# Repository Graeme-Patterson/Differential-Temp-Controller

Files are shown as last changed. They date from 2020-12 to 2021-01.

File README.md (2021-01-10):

# Differential-Temp-Controller

This is my differential temperature controller with Wi-Fi interface and Touch screen.

The idea behind this controller was to minimise the heating cost of keeping my workshop/mancave warm in Canberra Australia winters. After recently installing a solar electricity system on our house my thoughts were about how I could use the heat from the sun to warm my workshop.
The design was to heat air in long black plastic tubes mounted in a glass fronted box in a sunny location on the roof or wall of the workshop and use a low voltage fan to move air from outside, through the plastic tubes to warm the air and blow this into the workshop. To ensure that heating is achieved and to accound for any temperature drop getting the warmed air into the workshop, I needed a device that measured the temperature at the source and at the destination. I also wanted to have control over the device from inside my house and local control with visual display.

The final result uses a 2.8" ILI9341 TFT SPI display sourced from eBay (China) and an ESP8266/NodeMCU/ESP12-E device mounted on a custom PCB using a simple relay output to control a fan. Power is via a DC barrel connector (with ideas that this could be via Solar). The temperature sensors are low cost waterproof 10k NTC Thermistors, again sourced from eBay.

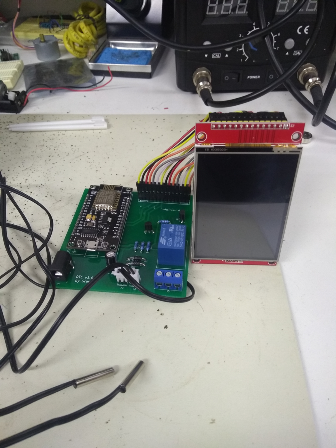
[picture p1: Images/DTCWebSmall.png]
DTC Pic

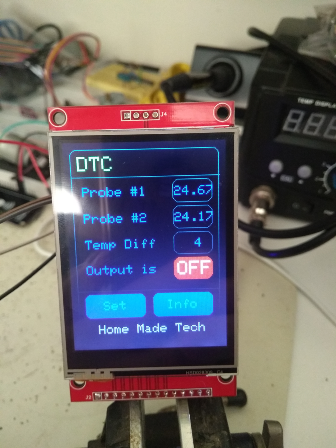
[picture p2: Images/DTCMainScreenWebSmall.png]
DTC Interface

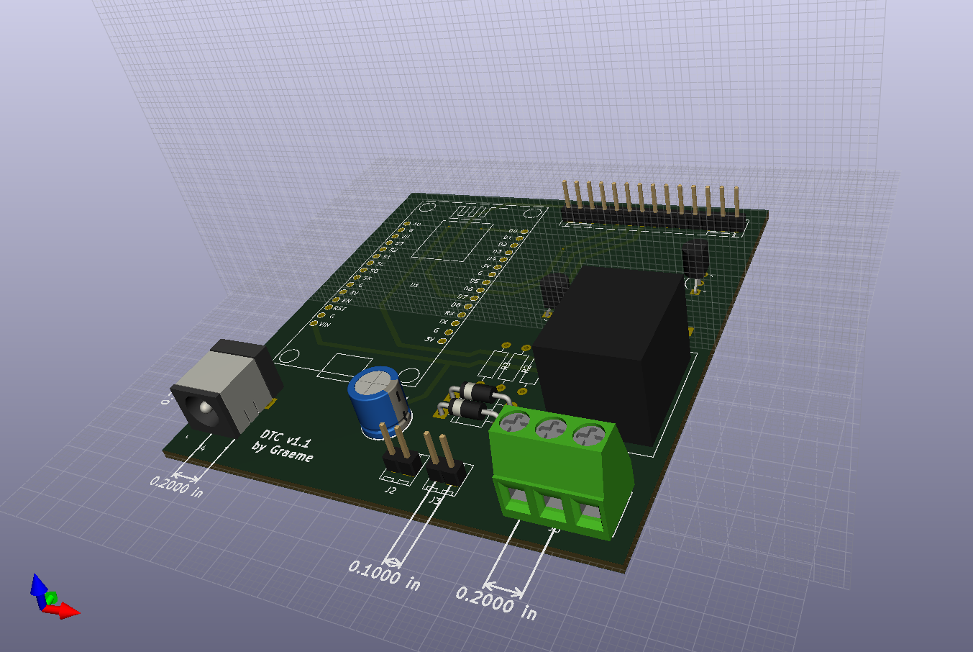
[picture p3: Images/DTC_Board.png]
3D View


- [DTC Overview](/README.md)
- [How to make one](/HowToMake.md)
- [Operation instructions](/Operation.md)
- [Connecting it up](/connecting.md)

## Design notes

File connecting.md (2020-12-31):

# Connecting it all up

Connect the DTC as follows:

Power the device from any DC source 5V source via the power supply jack. The jack will be centre pin positive.

NTC thermistors are plugged in to J2 and J3 on the PCB. Polarity is not important for these devices.

Connect your fan in series with the centre and left most pins on the 3 way connector relay output.

## A word of warning

If you choose to power the external fan from 110/240V via the onboard relay, **you do so at your own risk.** While the relay is rated for this voltage and the PCB traces have adequate separation from the other traces, this voltage is dangerous and should only be attempted by suitably qualified/experienced people.

- [DTC Overview](/README.md)
- [How to make one](/HowToMake.md)
- [Operation instructions](/Operation.md)
- [Connecting it up](/connecting.md)

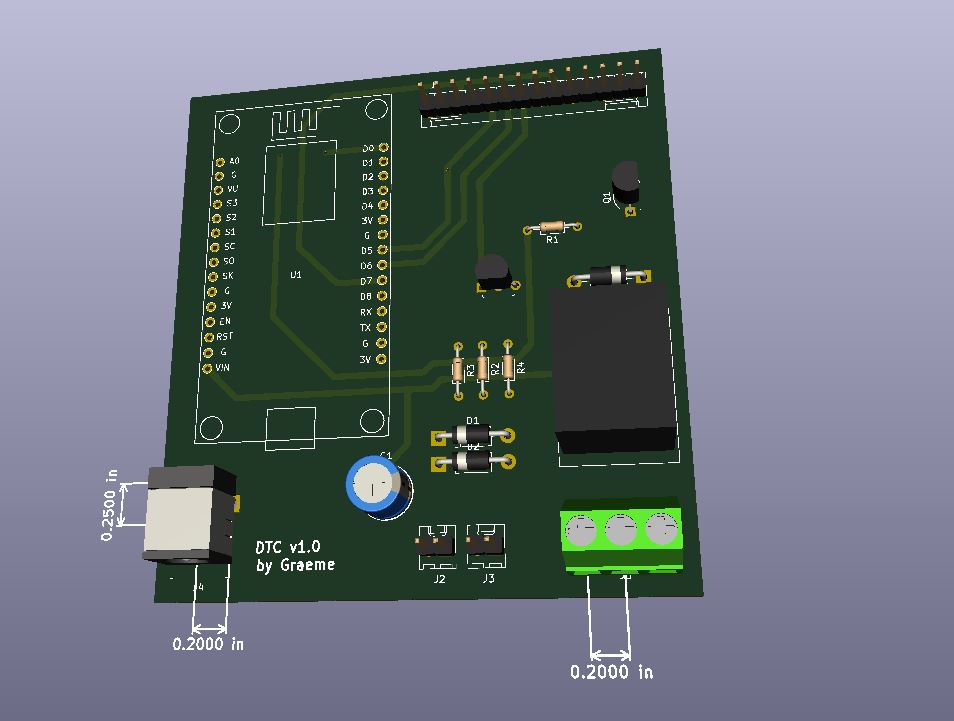
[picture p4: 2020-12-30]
PCB-KiCAD/DTC/Capture.JPG

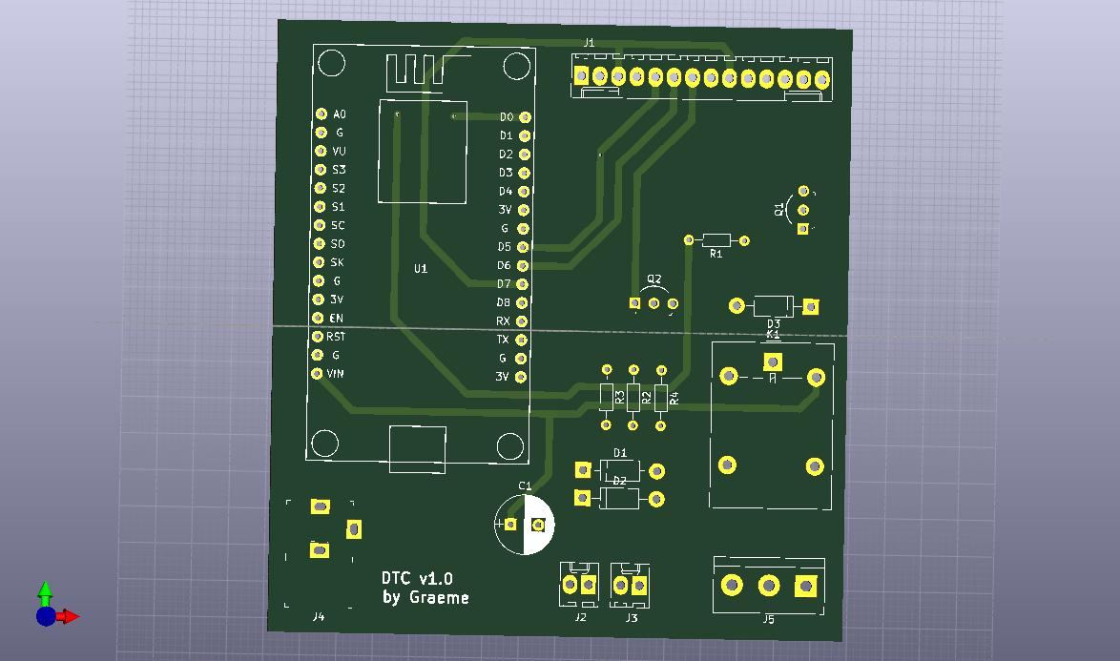
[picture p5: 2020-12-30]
PCB-KiCAD/DTC/The board.jpg

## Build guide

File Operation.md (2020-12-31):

# Operation

The DTC has only 3 screens availavle on the touch screen.

1. Main screen.
2. Set differential temp screen.
3. Information screen

When you are first using the DTC, you will need to start with the touch screen.

The main screen provides details of the temperatures of the two probes, the configured temperature difference as well as the current output status. In addition, you can access the Set screen and the Information screen.

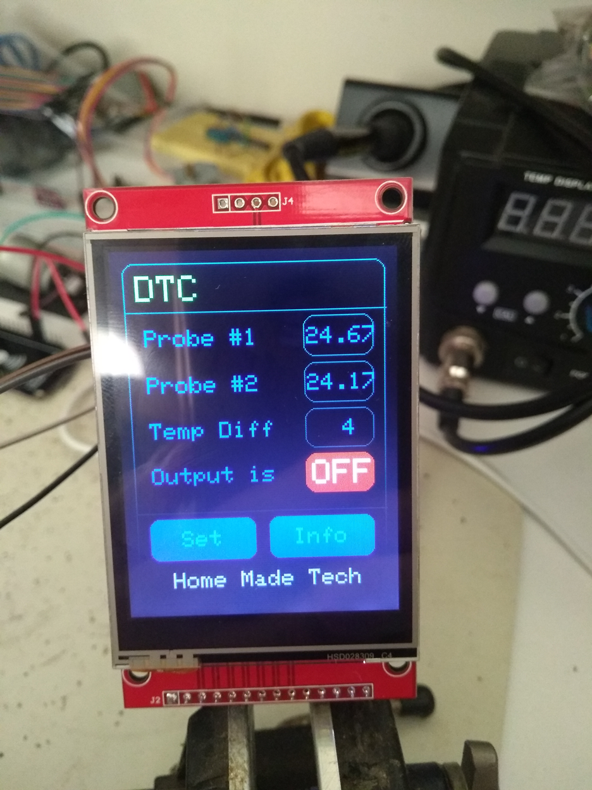
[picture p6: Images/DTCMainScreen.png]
Main screen


The Set differential temperature screen provides you the ability to adjust the temperature difference between the probes that will turn the output on. It is a simple up/down button operation with the "Save" button saving the value to memory. As expected the "Home" button will take you back to the main screen.

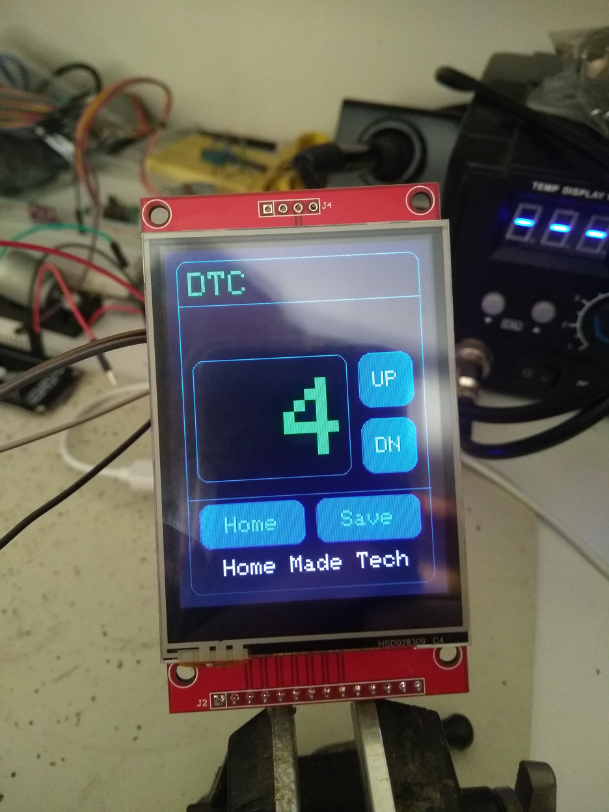
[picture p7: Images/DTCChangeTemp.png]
Set Differential Temperature Screen


The last screen is the Information screen. This screen provides you with easily accessible details allowing you to connect to the web interface from a browser and shows the chip Id which is used as a basic password allowing a user to configure the temperature differential from the browser. To connect to the web interface from a browser, simply type "http://\<IP Address>" into the address bar. 

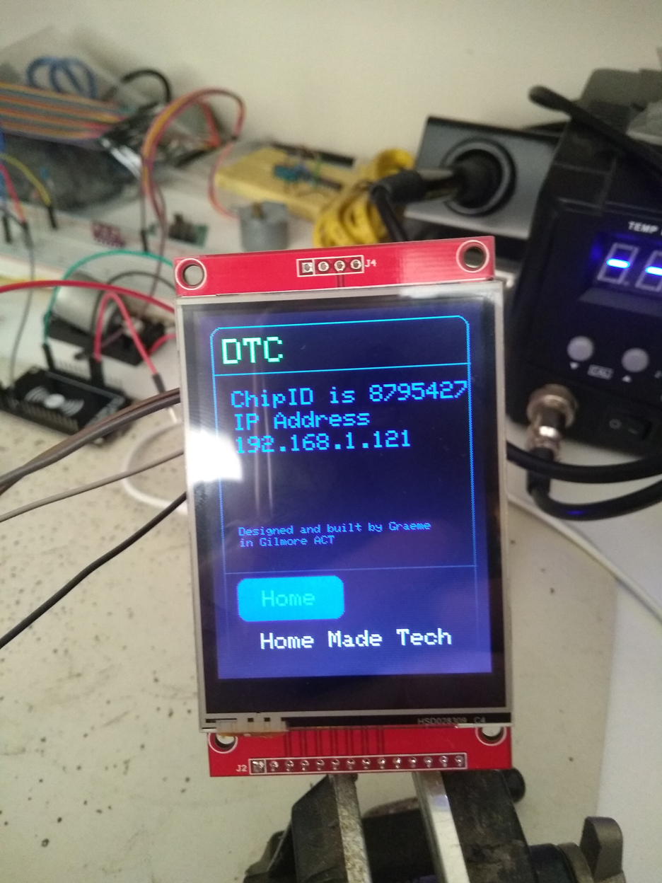
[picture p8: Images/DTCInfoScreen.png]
Information Screen


## Using the web interface

As was just mentioned, you will need to first obtain the IP address and Chip ID of the ESP device first and navigate to "http://\<IP Address>". Here you will be presented with a "functional" display allowing you to set the differential temperature of the controller only. 

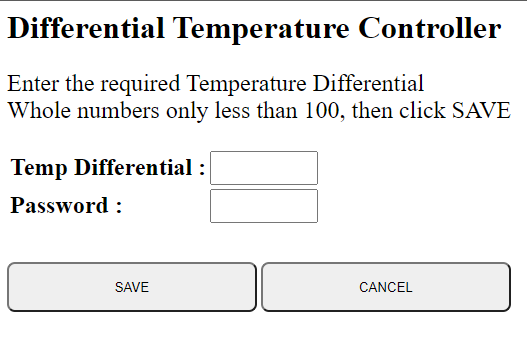
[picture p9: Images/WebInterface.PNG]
Web Interface


Simply enter the required temperature differential, enter the value of teh ChipId as the password and click save.
That's it. It's fairly simple and functional.

## A word of warning

If you choose to power the external fan from 110/240V via the onboard relay, **you do so at your own risk.** While the relay is rated for this voltage and the PCB traces have adequate separation from the other traces, this voltage is dangerous and should only be attempted by suitably qualified/experienced people.

- [DTC Overview](/README.md)
- [How to make one](/HowToMake.md)
- [Operation instructions](/Operation.md)
- [Connecting it up](/connecting.md)

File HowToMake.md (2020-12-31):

# How to make your DTC

You will need to gather all the required parts first.

Parts List

- 1 x ESP8266/NodeMCU/ESP12-E
- 3 x 1N4004 (or similar)  Diodes
- 1 x SRD-05VDC-SL-C SPDT 5V Relay
- 1 x DC-005 Power Supply Jack
- 2 x 10k NTC Waterproof Thermistor
- 1 x 2.8" TFT SPI LCD Touch Panel (ILI9341 240x320 5V/3.3V)
- 1 x BC337 transistor
- 1 x BC327 transistor
- 4 x 10k 1/4W MF ressitors
- 1 x 100uF 25V electrolytic capacitor
- 2 x 2 pin 0.1" pitch headers
- 1 x 14 pin 0.1" pitch header
- 1 x 3 way 0.2" pitch screw terminal
- 1 x PCB (you'll need to have this manufactured. I used JLCPCB - 5 boards for $2)

As I mentioned above, I used JLCPCB (https://jlcpcb.com) to have my PCB's made. They provided me with great service at an awesome price, $2 for 5 pcbs - double sided with solder mask and silk screened in your choice of colour.

Upload the DTCWiFiDisplay.ino sketch to your ESP8266.

Assemble the PCB as shown in [PCB Component Placement](/PCB/DTC_Component_Placement.pdf)

## First Run

On first run, the ESP device will not know about your WiFi network and will go into AP mode. Use you phone/laptop etc to connect to the ESP device AP and select/provide your WiFi network details. Restart the device and it should now be connected to your WiFi.

After you have your DTC on your WiFi network, take a look at [Operation instructions](/Operation.md) to see how to use it.

- [DTC Overview](/README.md)
- [How to make one](/HowToMake.md)
- [Operation instructions](/Operation.md)
- [Connecting it up](/connecting.md)

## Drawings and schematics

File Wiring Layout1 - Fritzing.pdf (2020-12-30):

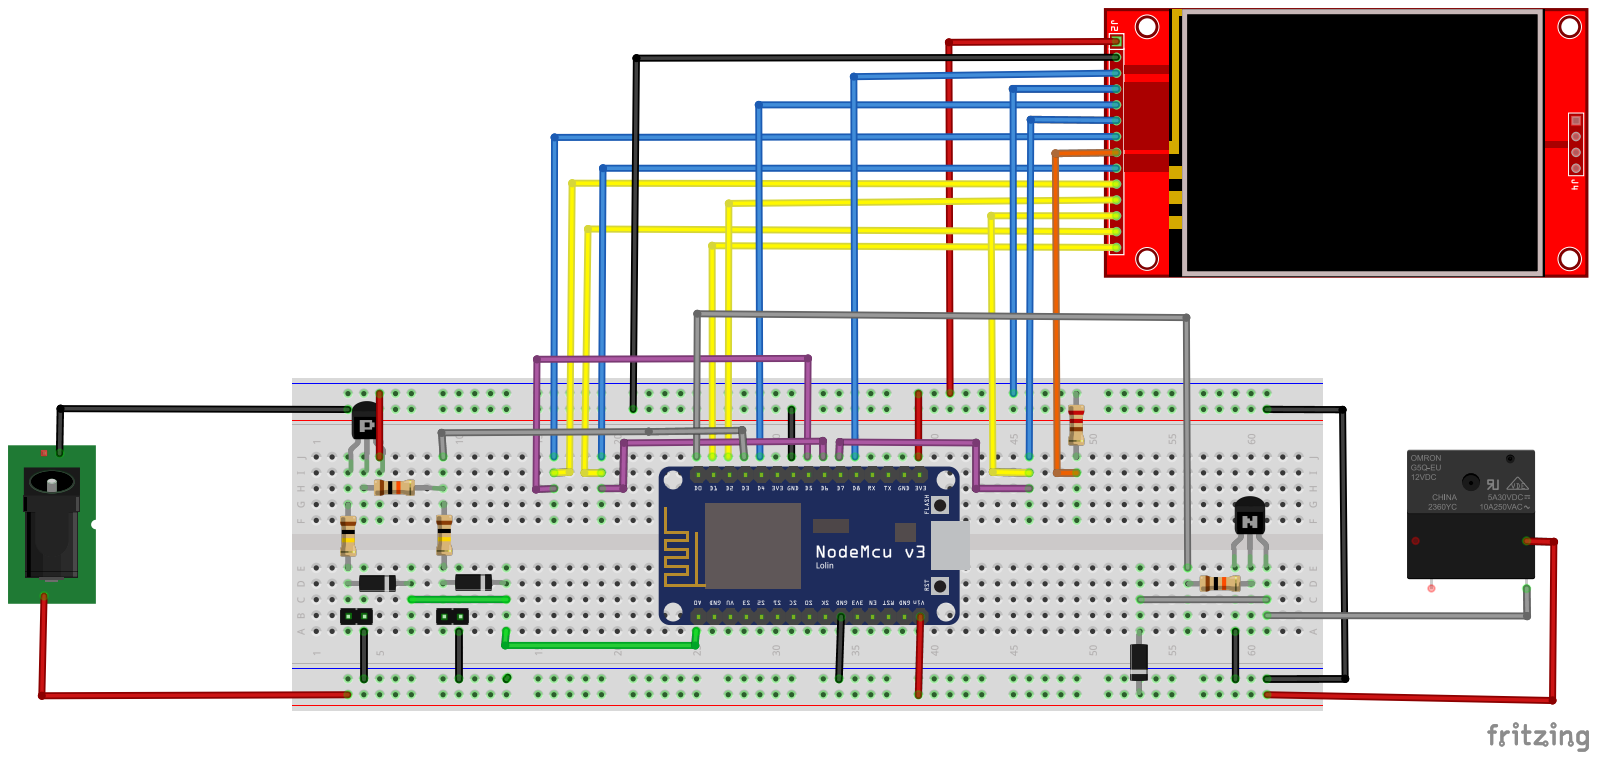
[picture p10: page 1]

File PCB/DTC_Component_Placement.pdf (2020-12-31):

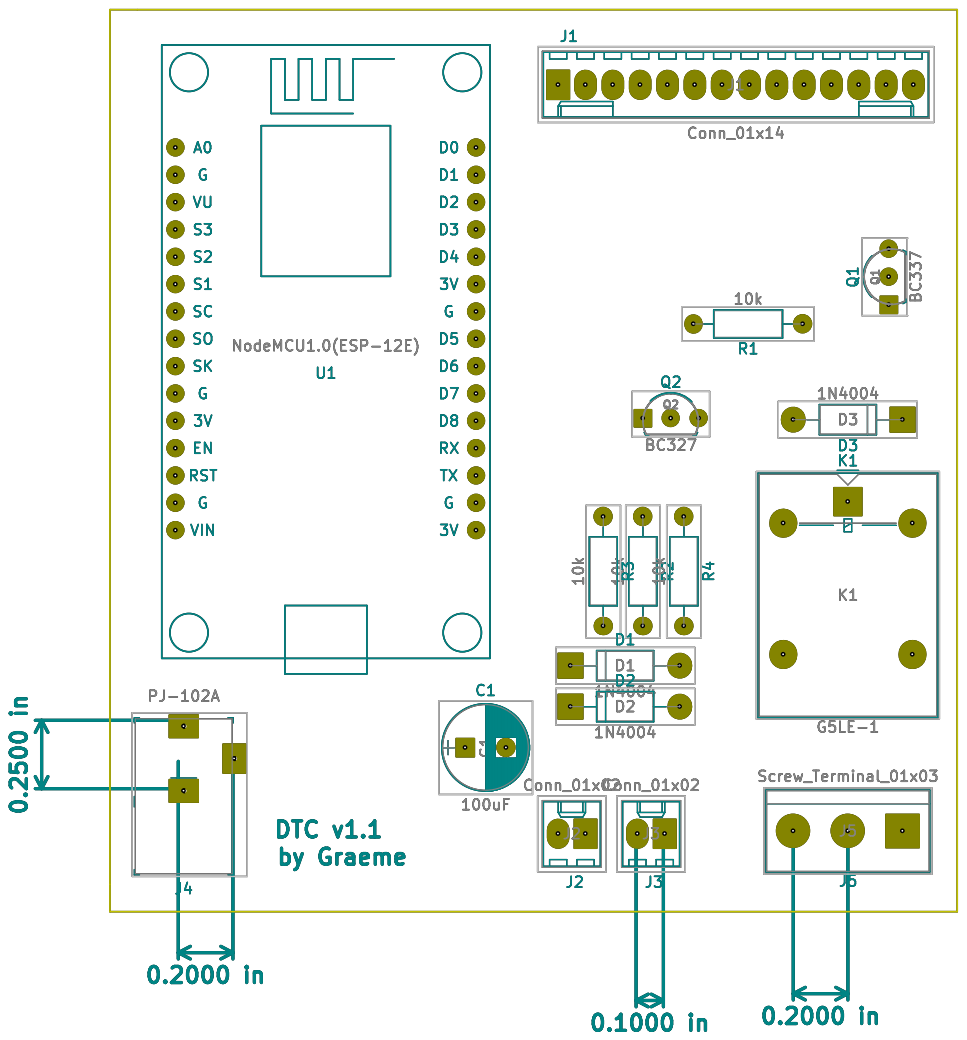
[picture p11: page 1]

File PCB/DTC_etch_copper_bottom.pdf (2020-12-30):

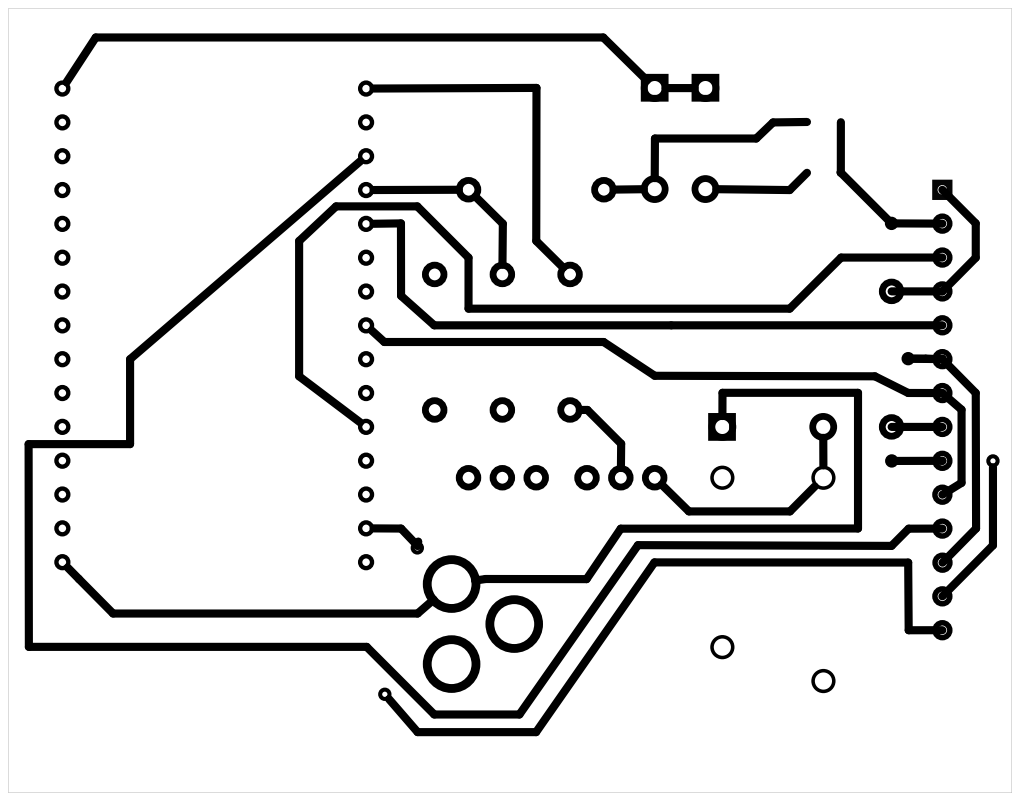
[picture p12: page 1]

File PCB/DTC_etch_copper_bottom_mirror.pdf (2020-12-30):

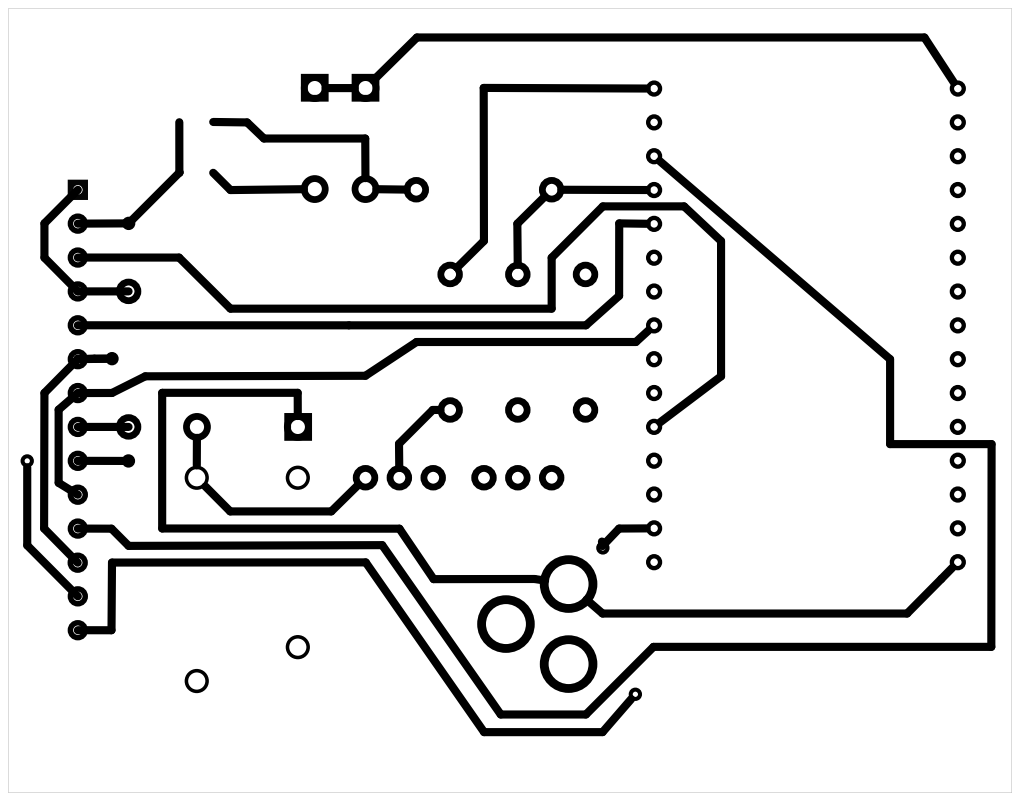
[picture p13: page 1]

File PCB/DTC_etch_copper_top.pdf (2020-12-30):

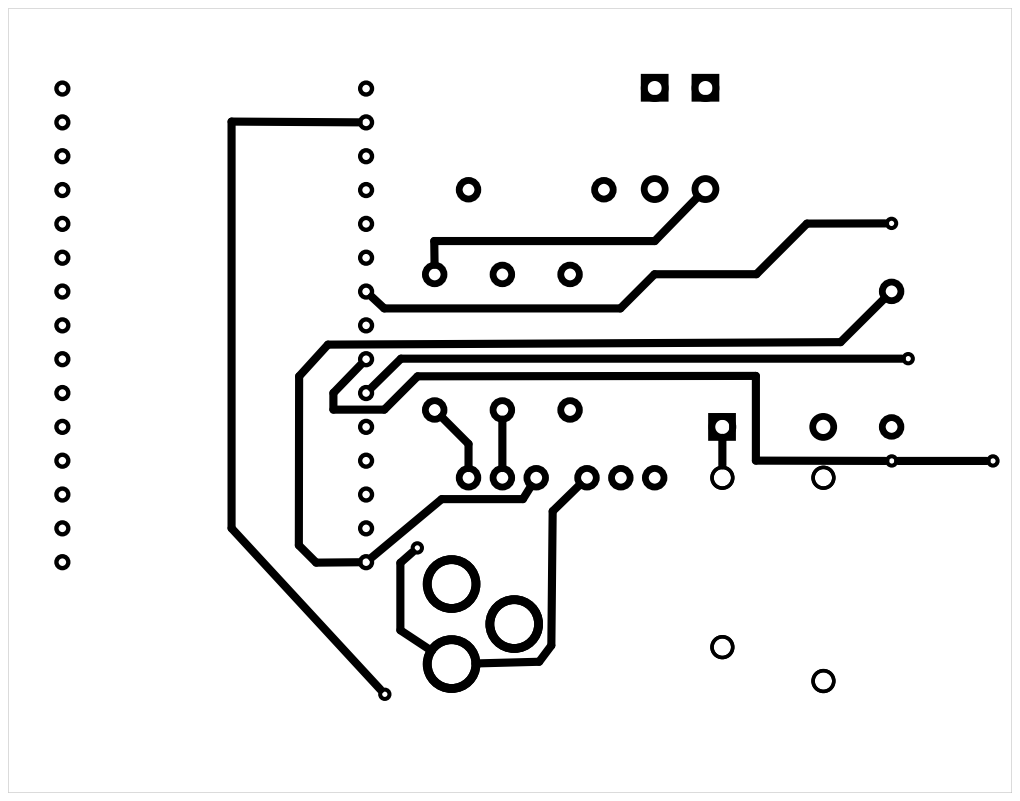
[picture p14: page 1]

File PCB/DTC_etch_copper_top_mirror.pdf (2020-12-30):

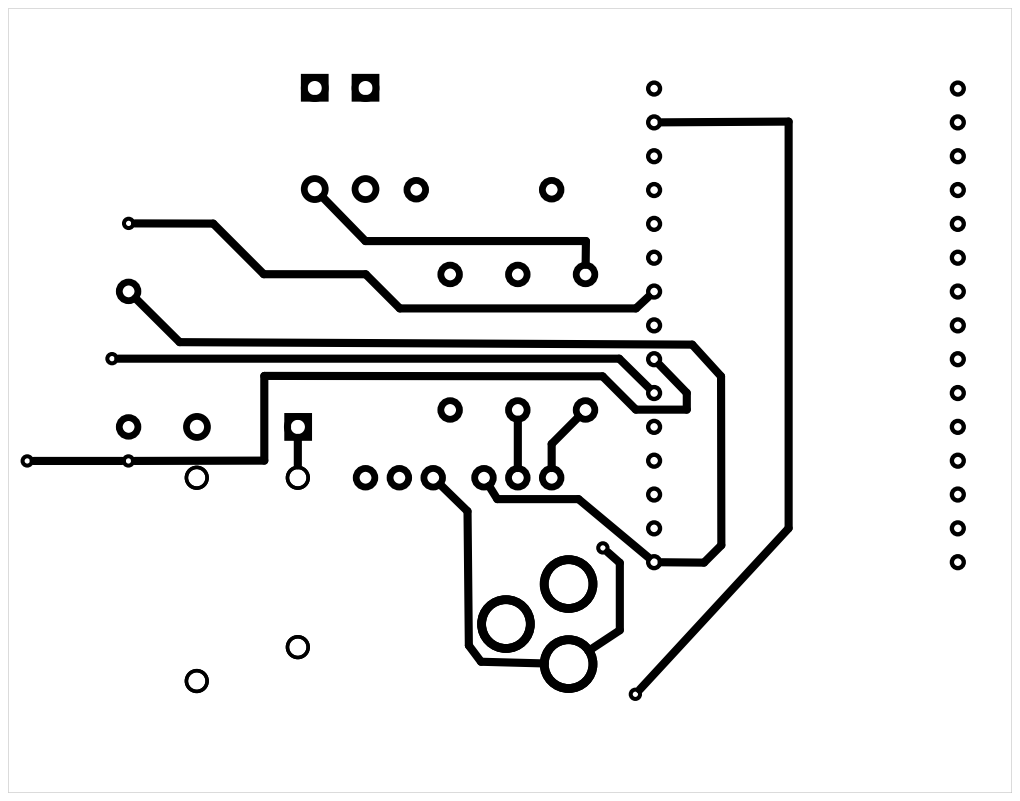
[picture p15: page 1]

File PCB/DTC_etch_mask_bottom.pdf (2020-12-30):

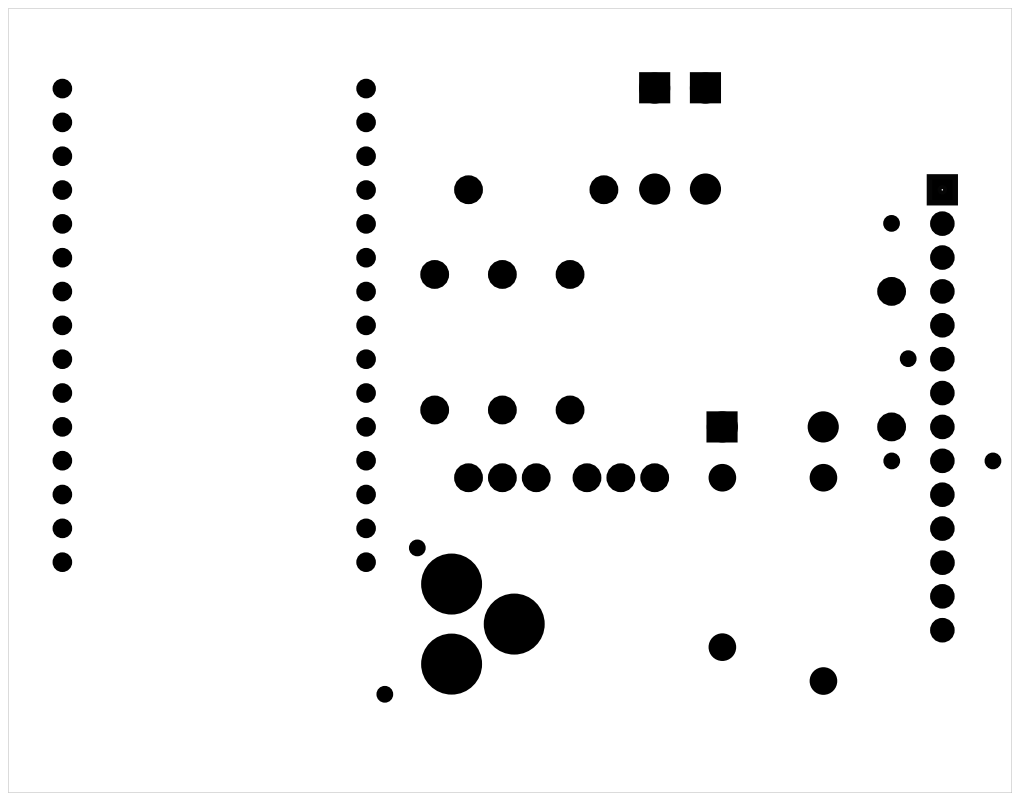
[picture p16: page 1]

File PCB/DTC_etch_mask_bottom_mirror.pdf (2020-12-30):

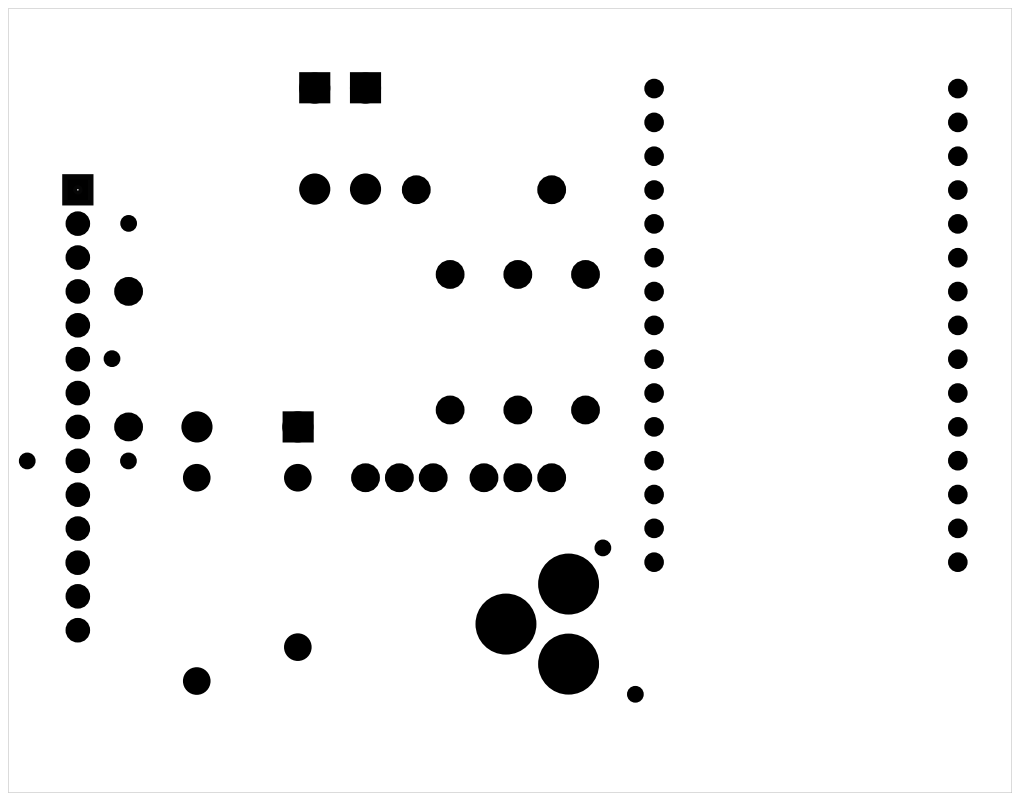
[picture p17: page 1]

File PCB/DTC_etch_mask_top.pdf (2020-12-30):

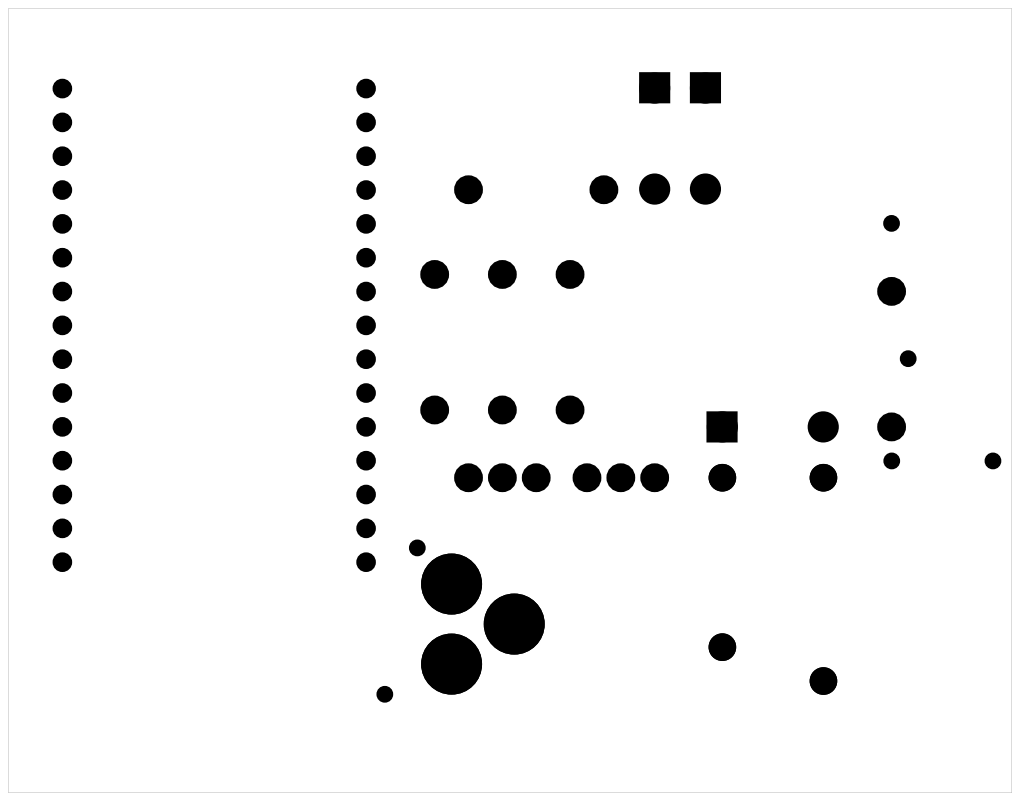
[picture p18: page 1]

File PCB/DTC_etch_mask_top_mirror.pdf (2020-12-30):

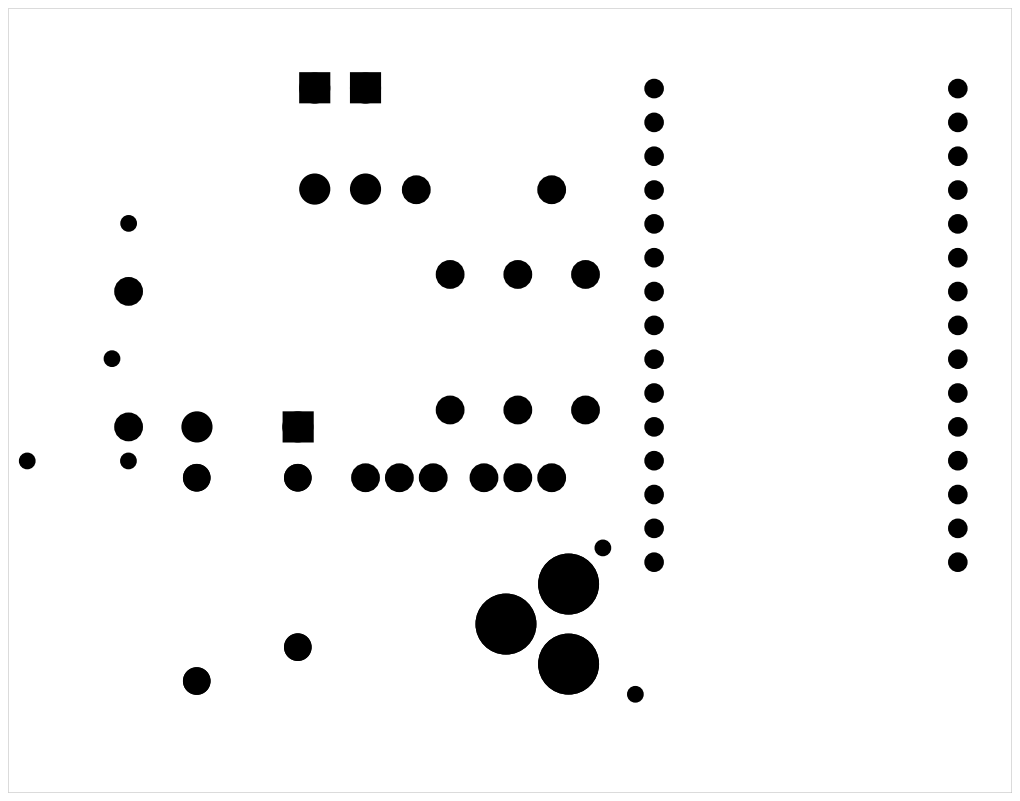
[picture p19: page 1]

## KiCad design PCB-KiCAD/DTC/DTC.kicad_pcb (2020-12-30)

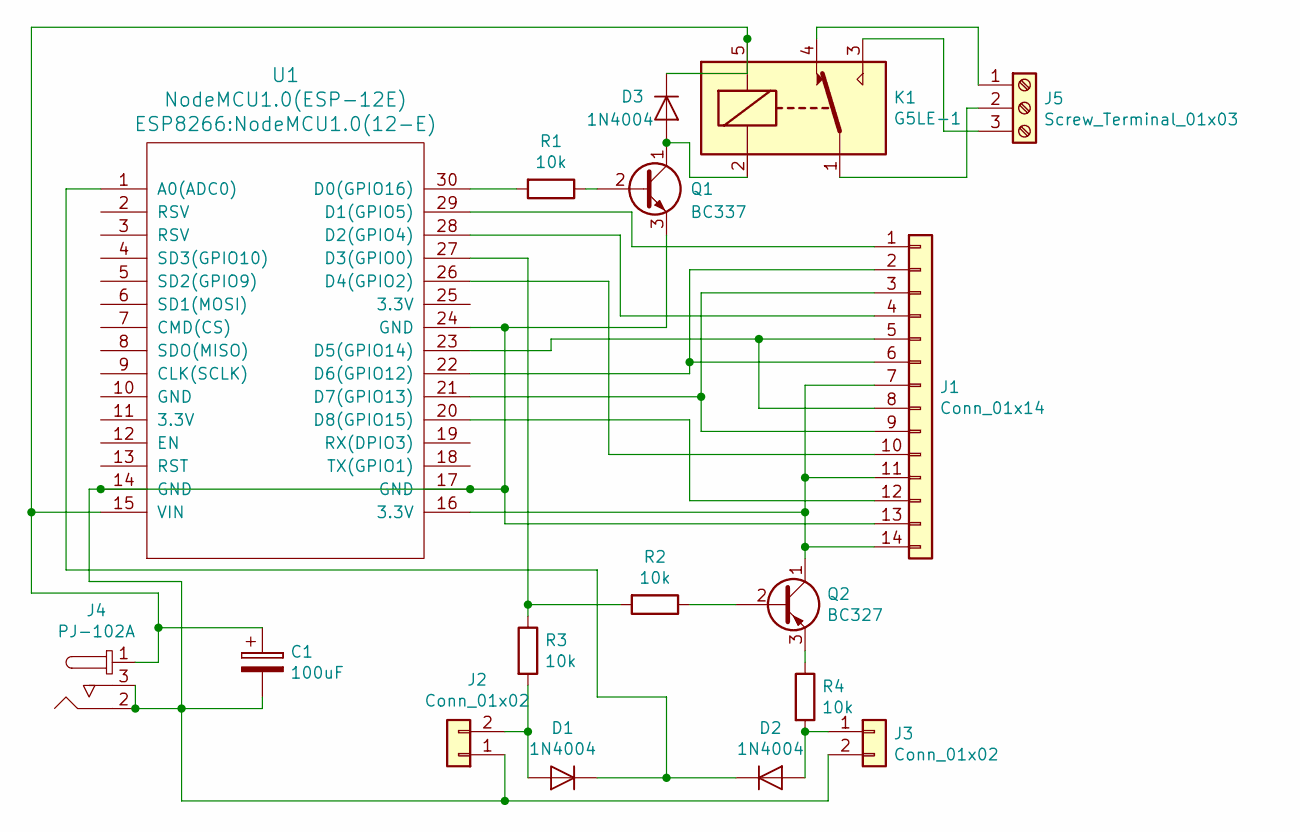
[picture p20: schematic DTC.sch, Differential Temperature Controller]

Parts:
C1: 100uF; CP_Radial_D8.0mm_P3.80mm
D1, D2, D3: 1N4004; D_DO-41_SOD81_P10.16mm_Horizontal
J1: Conn_01x14; Molex_KK-6410-14_14x2.54mm_Straight
J2, J3: Conn_01x02; Molex_KK-6410-02_02x2.54mm_Straight
J4: PJ-102A; Barrel_Jack_5.5mmODx2.1mmID_PJ-102A; MPN PJ-102A; Digi-Key_PN CP-102A-ND
J5: Screw_Terminal_01x03; TerminalBlock_bornier-3_P5.08mm
K1: G5LE-1; Relay_SPDT_OMRON-G5LE-1
Q1: BC337; TO-92-3_Formed_Leads
Q2: BC327; TO-92-3_Formed_Leads
R1, R2, R3, R4: 10k; R_Axial_DIN0204_L3.6mm_D1.6mm_P7.62mm_Horizontal
U1: NodeMCU1.0(ESP-12E); NodeMCU1.0(12-E)

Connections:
unnamed: C1.1, D3.1 (K), J4.1, K1.5, U1.15 (VIN)
unnamed: C1.2, J1.13, J2.1, J3.2, J4.2, J4.3, Q1.3 (E), U1.14 (GND), U1.17 (GND), U1.24 (GND)
unnamed: D1.1 (K), D2.1 (K), U1.1 (A0(ADC0))
unnamed: D1.2 (A), J2.2, R3.2
unnamed: D2.2 (A), J3.1, R4.2
unnamed: D3.2 (A), K1.2, Q1.1 (C)
unnamed: J1.1, U1.29 (D1(GPIO5))
unnamed: J1.2, J1.6, U1.22 (D6(GPIO12))
unnamed: J1.3, J1.9, U1.21 (D7(GPIO13))
unnamed: J1.4, U1.28 (D2(GPIO4))
unnamed: J1.5, J1.8, U1.23 (D5(GPIO14))
unnamed: J1.10, U1.26 (D4(GPIO2))
unnamed: J1.7, J1.11, J1.14, Q2.1 (C), U1.16 (3.3V)
unnamed: J1.12, U1.20 (D8(GPIO15))
unnamed: J5.1, K1.4
unnamed: J5.2, K1.1
unnamed: J5.3, K1.3
unnamed: Q1.2 (B), R1.1
unnamed: Q2.2 (B), R2.1
unnamed: Q2.3 (E), R4.1
unnamed: R1.2, U1.30 (D0(GPIO16))
unnamed: R2.2, R3.1, U1.27 (D3(GPIO0))

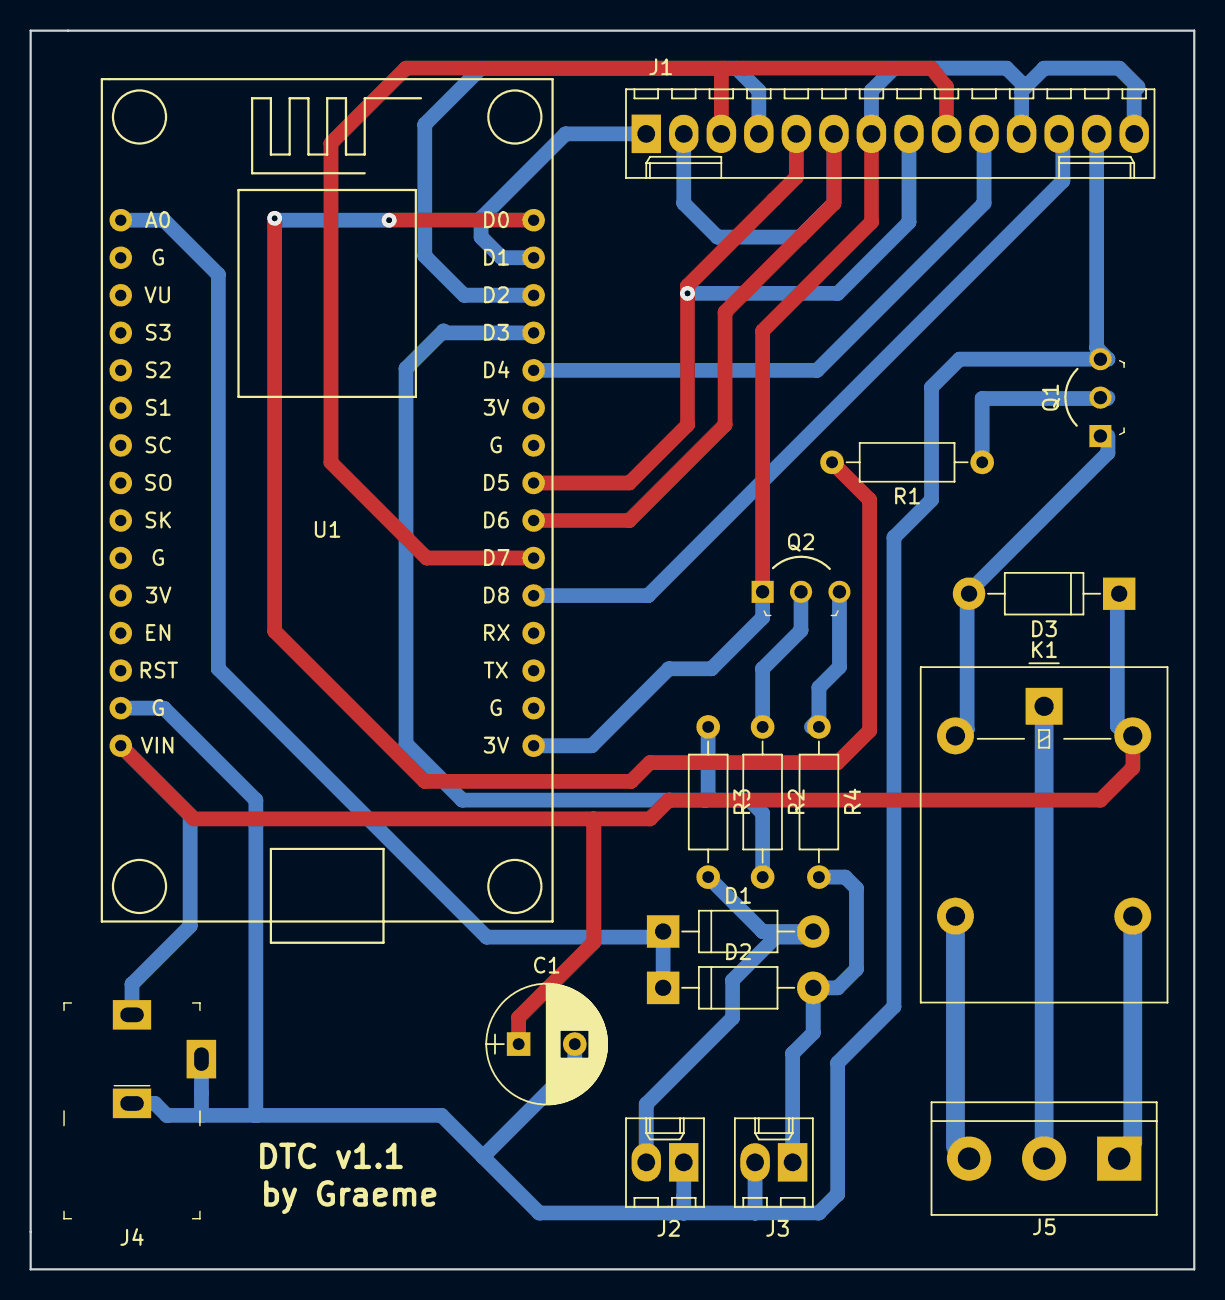
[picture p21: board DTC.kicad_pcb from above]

Board: 2 copper layers, 78.7 x 83.8 mm, 17 parts (0 on the bottom side), 22 nets.

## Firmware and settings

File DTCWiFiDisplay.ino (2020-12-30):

#include <ESP8266WiFi.h>          //https://github.com/esp8266/Arduino
#include <DNSServer.h>
#include <ESP8266WebServer.h>
#include <WiFiManager.h>          //https://github.com/tzapu/WiFiManager
#include <EEPROM.h>
#include <Arduino.h>
#include <SPI.h>
#include <Adafruit_ILI9341esp.h>
#include <Adafruit_GFX.h>
#include <XPT2046.h>

// which analog pin to connect
#define THERMISTORPIN A0         
// resistance at 25 degrees C
#define THERMISTORNOMINAL 10000      
// temp. for nominal resistance (almost always 25 C)
#define TEMPERATURENOMINAL 25   
// how many samples to take and average to smooth thing sout
#define NUMSAMPLES 5
// The beta coefficient of the thermistor (usually 3000-4000)
#define BCOEFFICIENT 3950
// the value of the 'other' resistor
#define SERIESRESISTOR 10000    
#define Thermistor0 0
#define Thermistor1 1
#define ThermistorSelect D3
//#define DIFFERENTIAL 5
#define DIODECOMPENSATION 100
#define RELAYOUTPUT D0
// For the esp shield, these are the default.
#define TFT_DC 2
#define TFT_CS 15
#define HOME 1
#define SET 2
#define INFO 3

Adafruit_ILI9341 tft = Adafruit_ILI9341(TFT_CS, TFT_DC);
XPT2046 touch(/*cs=*/ 4, /*irq=*/ 5);

Adafruit_GFX_Button homeButton;
Adafruit_GFX_Button upButton;
Adafruit_GFX_Button downButton;
Adafruit_GFX_Button saveButton;
Adafruit_GFX_Button setButton;
Adafruit_GFX_Button infoButton;

String webPage,notice,homeWebPage,message;
int DIFFERENTIAL;
int unsavedDifferential;
float Temp0;
float Temp1;
int samples[NUMSAMPLES];
int address = 0;
int relayState = 0;
int measurePeriod=10000;  // this is 10 seconds
unsigned long time_now = 0;
int screen = 1;
static uint16_t prev_x = 0xffff, prev_y = 0xffff;

ESP8266WebServer server(80);

const char htmlPage[]PROGMEM=R"=====(
<!DOCTYPE html>
<html><head><title>DTC-SET</title></head>
<body>
<h1>Differential Temperature Controller</h1><font size="5">
<FORM METHOD="POST" action="/Save">
<p> Enter the required Temperature Differential
<br> Whole numbers only less than 100, then click SAVE</p></font>
<table>
    <tr
        ><th style="font-size: 24px; text-align: left">Temp Differential : </th>
        <th><input type="text" size="4" name="myText" value="" autofocus style="font-size:24px;" ></th>
    </tr>
    <tr>
        <th style="font-size: 24px; text-align: left">Password          :</th>
        <th><input type="password" size="4" name="myCheck" value=""  style="font-size:24px"></th>
    </tr>
</table>
<br><br>
<th><input type="submit" value="SAVE" style="height:50px; width:250px;border-radius: 8px"></th>
<input type="button" value="CANCEL" style="height:50px; width:250px;border-radius: 8px" onclick="location.href='/'" />
</form>
</body>
</html>
)=====";

void handleRoot()
{
  homeWebPage = "<!DOCTYPE html><html><head><title>DTC</title><meta http-equiv=\"refresh\" content=\"30\" /></head><body><h1>Differential Temperature Controller</h1><font size=\"5\"><p><pre>Temp Sensor 0     : ";
  homeWebPage += Temp0;
  homeWebPage += "<br>Temp Sensor 1     : ";
  homeWebPage += Temp1;
  homeWebPage += "<br>Temp Differential : ";
  homeWebPage += DIFFERENTIAL;
  homeWebPage += "<br>Output State is   :";
  if(relayState)
  {
    homeWebPage += "<button style=\"height:25px; width:60px; border-radius: 8px; color: white; background-color: green\" >ON</button>";
  }
  else
  {
    homeWebPage += "<button style=\"height:25px; width:60px; border-radius: 8px; color: white; background-color: red\" >OFF</button>";
  }
  homeWebPage += "<br></font><font size=\"5\" color=\"red\">";
  homeWebPage += message;
  homeWebPage += "</font><br><button style=\"height:50px; width:250px; border-radius: 8px\" onclick=\"location.href='/postForm'\">SET TEMP DIFFERENTIAL</button></body></html>"; // need to escape '\' the " characters
  server.send(200,"text/html",homeWebPage);
}

void handlePostForm()
{
  webPage=htmlPage;
  server.send(200,"text/html",webPage);
}

void handleSave()
{
  int tempEntered;
  Serial.println("=========================================================");
  Serial.println("Text Value = " + server.arg("myText"));
  tempEntered = (server.arg("myText")).toInt();
  //DIFFERENTIAL += 10;  // This just proves that I can use the integer
  Serial.println(tempEntered);
  if(server.arg("myCheck") != (String(ESP.getChipId()).c_str()))
  {
    message = "Password is incorrect!";
  }
  else if(tempEntered == 0)
  {
    Serial.println("Value entered wasn't a number");
    message = "Value entered wasn't a number";
  }
  else if ((tempEntered < -100) || (tempEntered > 100))
  {
    Serial.println("Value entered was to large");
    message = "Temp differential entered was to large (needs to be < 100)";
  }
  else if ((tempEntered <= 100) && (tempEntered >= -100))  // this ensures the FLASH used will only be 1 byte.
  {
    DIFFERENTIAL = tempEntered;
    EEPROM.write(address, DIFFERENTIAL);
    EEPROM.commit();
    message = "";
    delay(100);   // give it time to do what's required
  }
  server.sendHeader("Location","/");
  server.send(303);
}

void handleNotFound()
{
  server.send(404, "text/plain", "404: Not found"); // Send HTTP status 404 (Not Found) when there's no handler for the URI in the request
}

void setup() 
{
  Serial.begin(115200);
  pinMode(ThermistorSelect, OUTPUT);
  pinMode(RELAYOUTPUT, OUTPUT);  
  EEPROM.begin(512);
  DIFFERENTIAL = EEPROM.read(address);  //get the initial stored value after reboot
    
  WiFiManager wifiManager;
  //reset settings - for testing
  //wifiManager.resetSettings();

  wifiManager.setTimeout(180);
  
  if(!wifiManager.autoConnect("DTCDevice")) 
  {
    Serial.println("failed to connect and hit timeout");
    delay(3000);
    //reset and try again, or maybe put it to deep sleep
    ESP.reset();
    delay(5000);
  } 

  //if you get here you have connected to the WiFi
  Serial.print("connected to selected WiFi access point with IP Address ");
  Serial.println(WiFi.localIP());
  message = "";
  server.on("/", HTTP_GET, handleRoot);
  server.on("/postForm",handlePostForm);  // tells server what function to call for the selected url
  server.on("/Save",handleSave);
  server.onNotFound(handleNotFound);        // When a client requests an unknown URI (i.e. something other than "/"), call function "handleNotFound"
  server.begin(); // starts the web server
  Serial.println("============================================");
  Serial.println(String(ESP.getChipId()).c_str());
  Serial.println("============================================");
  SPI.setFrequency(ESP_SPI_FREQ);
  tft.begin();
  touch.begin(tft.width(), tft.height());  // Must be done before setting rotation
  Serial.print("tftx ="); Serial.print(tft.width()); Serial.print(" tfty ="); Serial.println(tft.height());
  tft.fillScreen(ILI9341_BLACK);
  // Replace these for your screen module
  touch.setCalibration(1951, 128, 169, 1915);
  drawHome();
  delay(10000);
}

void loop() 
{
  server.handleClient();   // handles web requests
  float average;
  uint16_t x, y;  // used for touch screen input

  if(millis()> time_now + measurePeriod)
  {
    time_now = millis();
    // Get Thermistor0 temp
    average = getTemp(Thermistor0);
    Temp0 = convertToTemp(average);  
    // Get Thermistor1 temp
    average = getTemp(Thermistor1);
    Temp1 = convertToTemp(average);
    // set relay state
    if((Temp1 - Temp0)>DIFFERENTIAL)
    {
      relayState = 1;
    }
    else
    {
      relayState = 0;
    }
    // write to relay output
    Serial.println("============================================");
    Serial.print("Differential value : ");
    Serial.println(Temp1 - Temp0);
    digitalWrite(RELAYOUTPUT,relayState);
 
    Serial.println("============================================");
    Serial.println(String(ESP.getChipId()).c_str());
    Serial.println("============================================");
    if(screen == HOME)
    { 
      updateHome();
    }
  }
//============================================================
if (touch.isTouching()) 
  {
    touch.getPosition(x, y);
    prev_x = x;
    prev_y = y;
  } 
  else 
  {
    prev_x = prev_y = x = y = 0xffff;
  }

  if (screen == HOME)
  {
    // Check if a button is being pressed.
    setButton.press(setButton.contains(x, y)); // tell the button it is pressed 
    infoButton.press(infoButton.contains(x,y));
    // now we can ask the buttons if their state has changed
    if (setButton.justReleased()) { unsavedDifferential = DIFFERENTIAL; drawSetScreen();}
    if (setButton.justPressed()) { setButton.drawButton(true);} // draw invert!       
    if (infoButton.justReleased()) { drawInfo();} 
    if (infoButton.justPressed()) { infoButton.drawButton(true);} // draw invert!  
  }
  else if (screen == SET)
  {
    // Check if a button is being pressed.
    homeButton.press(homeButton.contains(x, y)); // tell the button it is pressed
    upButton.press(upButton.contains(x, y)); // tell the button it is pressed
    downButton.press(downButton.contains(x, y)); // tell the button it is pressed
    saveButton.press(saveButton.contains(x, y)); // tell the button it is pressed
  
    // now we can ask the buttons if their state has changed
    if (homeButton.justReleased()) {drawHome();} 
    if (homeButton.justPressed()) { homeButton.drawButton(true);} // draw invert!
    if (upButton.justReleased()) { printDifferential(); upButton.drawButton();} // draw normal
    if (upButton.justPressed()) { unsavedDifferential += 1; upButton.drawButton(true);} // draw invert!
    if (downButton.justReleased()) { printDifferential(); downButton.drawButton();} // draw normal
    if (downButton.justPressed()) { unsavedDifferential -= 1; downButton.drawButton(true);} // draw invert!
    if (saveButton.justReleased()) 
    { 
      // save the unsavedDifferential to DIFFERENTIAL and store
      DIFFERENTIAL = unsavedDifferential;
      EEPROM.write(address, DIFFERENTIAL);
      EEPROM.commit();
      delay(100);   // give it time to do what's required
      saveButton.drawButton(); // draw normal
    } 
    if (saveButton.justPressed()) { saveButton.drawButton(true);} // draw invert!
  }
  else if (screen == INFO)
  {
    // Check if a button is being pressed.
    homeButton.press(homeButton.contains(x, y)); // tell the button it is pressed
    upButton.press(upButton.contains(x, y)); // tell the button it is pressed
    if (homeButton.justReleased()) {drawHome();} 
    if (homeButton.justPressed()) { homeButton.drawButton(true);} // draw invert!        
  }
  delay(20);
}

float getTemp(int Thermistor)
{
  uint8_t i;
  float average;

  digitalWrite(ThermistorSelect, Thermistor);
  delay(10);
  // take N samples in a row, with a slight delay
  for (i=0; i< NUMSAMPLES; i++) 
  {
   samples[i] = analogRead(THERMISTORPIN);
   delay(10);
  }
  
  // average all the samples out
  average = 0;
  for (i=0; i< NUMSAMPLES; i++) 
  {
     average += samples[i];
  }
  average /= NUMSAMPLES;
  average += DIODECOMPENSATION;
  Serial.println("============================================");
  Serial.print("Average analog reading on Thermistor "); 
  Serial.print(Thermistor);
  Serial.print(" ");
  Serial.println(average);
  // convert the value to resistance
  average = 1023 / average - 1;
  average = SERIESRESISTOR / average;
  Serial.print("Resistance of Thermistor "); 
  Serial.print(Thermistor);
  Serial.print(" ");
  Serial.println(average);  
  return average;
}

float convertToTemp(float average)
{
  float steinhart;
  steinhart = average / THERMISTORNOMINAL;     // (R/Ro)
  steinhart = log(steinhart);                  // ln(R/Ro)
  steinhart /= BCOEFFICIENT;                   // 1/B * ln(R/Ro)
  steinhart += 1.0 / (TEMPERATURENOMINAL + 273.15); // + (1/To)
  steinhart = 1.0 / steinhart;                 // Invert
  steinhart -= 273.15;                         // In Kelvin, convert to C  
  Serial.print("Temperature "); 
  Serial.print(steinhart);
  Serial.println(" *C");
  Serial.println("============================================");
  return steinhart;
}

void updateHome()
{
  tft.setTextColor(ILI9341_BLUE);
  tft.setTextSize(2);
  tft.fillRoundRect(160,55,60,35,10, ILI9341_BLACK);
  tft.drawRoundRect(160,55,60,35,10, ILI9341_DARKCYAN);
  tft.fillRoundRect(160,95,60,35,10, ILI9341_BLACK);
  tft.drawRoundRect(160,95,60,35,10, ILI9341_DARKCYAN); 
  tft.fillRoundRect(160,135,60,35,10, ILI9341_BLACK);
  tft.drawRoundRect(160,135,60,35,10, ILI9341_DARKCYAN);   
  
  tft.setCursor(162, 65);
  tft.println(Temp0);
  tft.setCursor(162, 105);
  tft.println(Temp1);  
  tft.setCursor(180,145);
  if(DIFFERENTIAL < 10){tft.print(" ");}
  tft.println(DIFFERENTIAL);  
  
  tft.setTextColor(ILI9341_WHITE);
  if(relayState)
  {
    tft.fillRoundRect(160, 175, 60, 35, 10, ILI9341_DARKGREEN);
    tft.setCursor(167,179);
    tft.setTextSize(4);
    tft.print("ON");
  }
  else
  {
    tft.fillRoundRect(160, 175, 60, 35, 10, ILI9341_RED);
    tft.setCursor(165,181);
    tft.setTextSize(3);
    tft.print("OFF");
  }
}

void drawHome()
{
  HomeMadeTech();
  screen = HOME;
  setButton.initButtonUL(&tft, 20, 230, 95, 40, ILI9341_DARKCYAN, ILI9341_BLUE, ILI9341_GREENYELLOW, "Set", 2);
  setButton.drawButton();
  infoButton.initButtonUL(&tft, 125, 230, 95, 40, ILI9341_DARKCYAN, ILI9341_BLUE, ILI9341_GREENYELLOW, "Info", 2);
  infoButton.drawButton();
  tft.setTextColor(ILI9341_BLUE);
  tft.setTextSize(2);
  tft.setCursor(25, 65);
  tft.println("Probe #1");
  tft.setCursor(25, 105);
  tft.println("Probe #2");
  tft.setCursor(25, 145);
  tft.println("Temp Diff ");
  tft.setCursor(25, 185);
  tft.print("Output is");
  updateHome();
}

void drawSetScreen()
{
  HomeMadeTech();
  screen = SET;
  homeButton.initButtonUL(&tft, 20, 230, 95, 40, ILI9341_DARKCYAN, ILI9341_BLUE, ILI9341_GREENYELLOW, "Home", 2);
  upButton.initButtonUL(&tft, 170, 100, 50, 50, ILI9341_DARKCYAN, ILI9341_BLUE, ILI9341_GREENYELLOW, "UP", 2);
  downButton.initButtonUL(&tft, 170, 160, 50, 50, ILI9341_DARKCYAN, ILI9341_BLUE, ILI9341_GREENYELLOW, "DN", 2);
  saveButton.initButtonUL(&tft, 125, 230, 95, 40, ILI9341_DARKCYAN, ILI9341_BLUE, ILI9341_GREENYELLOW, "Save", 2);
  homeButton.drawButton();
  upButton.drawButton();
  downButton.drawButton();
  saveButton.drawButton();
  tft.drawRoundRect(20, 100, 140, 110, 10, ILI9341_DARKCYAN);
  printDifferential();
}

void drawInfo()
{
  HomeMadeTech();
  screen = INFO; 
  homeButton.initButtonUL(&tft, 20, 230, 95, 40, ILI9341_DARKCYAN, ILI9341_BLUE, ILI9341_GREENYELLOW, "Home", 2);
  homeButton.drawButton(); 
  tft.setTextColor(ILI9341_BLUE);
  tft.setCursor(25, 65);
  tft.print("ChipID is ");
  tft.println(String(ESP.getChipId()).c_str());
  tft.setCursor(25, 85);
  tft.println("IP Address ");
  tft.setCursor(25, 105);
  tft.println(WiFi.localIP());
  tft.setCursor(25, 185);
  tft.setTextSize(1);
  tft.println("Designed and built by Graeme");
  tft.setCursor(25, 195);
  tft.println("in Gilmore ACT");
}
void printDifferential()
{
  if(unsavedDifferential >= 20){unsavedDifferential = 20; tft.setTextColor(ILI9341_RED);}
  if(unsavedDifferential <= 0){unsavedDifferential = 0; tft.setTextColor(ILI9341_RED);}
  else {tft.setTextColor(ILI9341_GREEN);}
  tft.setCursor(40, 120);
  tft.setTextSize(10);
  tft.fillRoundRect(25, 105, 130, 100,10, ILI9341_BLACK);
  if(unsavedDifferential < 10) { tft.print(" ");}
  tft.print(unsavedDifferential);
}

void HomeMadeTech()
{
  tft.fillScreen(ILI9341_BLACK);
  tft.drawRoundRect(10, 10, 220, 300, 10, ILI9341_DARKCYAN);
  tft.drawLine(10,50,230,50,ILI9341_DARKCYAN);
  tft.drawLine(10,225,230,225,ILI9341_DARKCYAN);
  tft.setCursor(20, 20);
  tft.setTextSize(3);
  tft.setTextColor(ILI9341_GREEN);
  tft.print("DTC  ");
  tft.setTextColor(ILI9341_WHITE);
  tft.setTextSize(2);
  tft.setCursor(40,280);
  tft.println("Home Made Tech");
}

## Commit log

2020-12-30 Added PCB Files
    KiCAD PCB files
    [DTC.kicad_pcb, DTC.sch]
2020-12-30 Updated PCB
    Updated PCB and added pdf's of layers
    [DTC-B.Cu.gbr, DTC-B.Mask.gbr, DTC-B.SilkS.gbr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]
